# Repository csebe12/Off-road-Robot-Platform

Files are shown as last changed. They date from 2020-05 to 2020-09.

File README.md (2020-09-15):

# Off-road-Robot-Platform
This repository contains the instructions and code to set up an off-road tracked platform using DFRobot's Yuewalker chassis.

This is how the assembled robot will look like:


The webserver was developed to be mobile friendly. The following pictures show how the UI looks like on desktop (top view) and on a mobile device (bottom view).

## Control panel
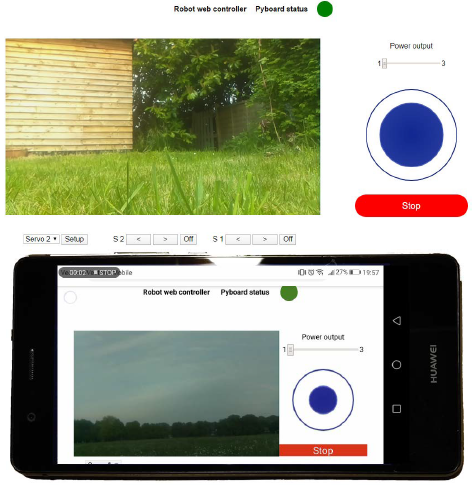
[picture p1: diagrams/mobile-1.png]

The first panel is the control panel. On the top, the green circle indicates that the UART communication between the Raspberry Pi and Pyboard works properly. If there is an error, it will turn red. The live camera feed is displayed on the left. The robot can be controlled by the blue joystick on the right. The output from the joystick is transformed into left and right motor values using the arcade mixing function. The different power settings enable precise and fast movements. On the bottom, the servos can be setup on the go. Once the user clicks setup, the servo can be plugged in into the corresponding port and it can be controlled using the two arrows. Servos can be deinitialized by clicking the off button.

## Navigation panel
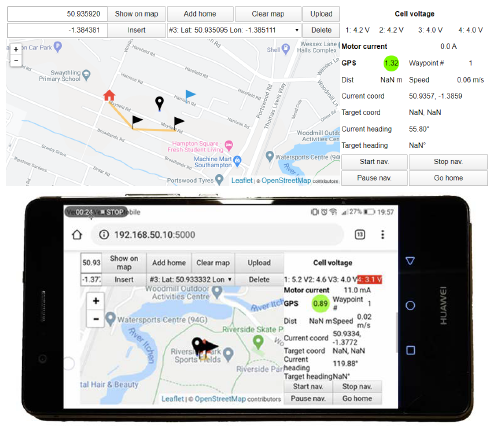
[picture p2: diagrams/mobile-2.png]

The second panel is used for setting up and monitoring the autonomous mode. The map is displayed using the Leaflet JavaScript library. The map tiles were downloaded using the RgoogleMaps package and are stored on the Raspberry Pi. This enables the users to use the map without internet connection. Waypoints can either be added by entering their latitude and longitude or simply by clicking on the map. The waypoint can then be added to the list by clicking insert. Any waypoint can be removed from or added to the list, or can be set as home. Waypoints are uploaded to the Pyboard by clicking the upload button. Data such as the battery voltage, the motor’s current consumption and navigation information are displayed on the right. When the navigation is started the bottom four buttons will have the same colours as the LEDs.

## Command history
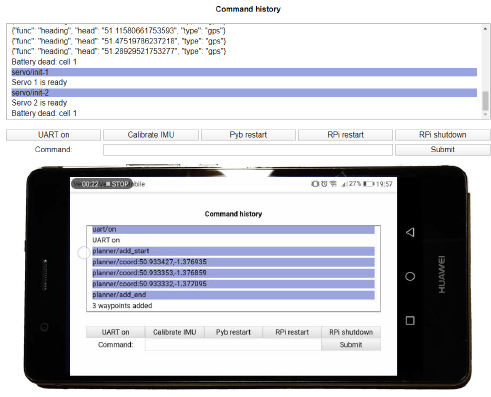
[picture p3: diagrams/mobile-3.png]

The third panel shows the command history. To distinguish between the Pyboard’s and the Rasperry Pi’s messages, those sent by the Raspberry Pi have a blue background. The most popular actions can be called by clicking the buttons, or the user can issue any command by entering it to the input box.

# Setup
## Hardware
The robot uses two MCUs, a Pyboard v1.1 and a Raspberry Pi Zero W. The latter can be exchanged to any WiFi enabled Raspberry Pi.
The schematic, layout and bill of materials to assemble the control unit can be found in the control-unit folder.
## Pyboard
The application requires threads and double precision floating points. To achieve this, the firmware needs to be updated from [the official website](https://micropython.org/download/pybv1/).
The code is located in the micropython folder. Without precompilation, its size too big to store on the Pyboard's flash, so an SD card is required.
### SD card booting
The SD card cannot be directly mounted on startup, because the buck converter cannot handle the sudden current surge. To fix this, put the pybrestart.py file on the flash. This will do a hard reset after 3 seconds. Then the SD card will be mounted.
### Files
Upload all the files from the micropython folder to the Pyboard's SD card except for the pybrestart.py
## Raspberry Pi
### [Enable I2C and SSH](https://itsfoss.com/ssh-into-raspberry/)
### Install Flask
```
sudo pip install flask + pip install -U flask-cors
```
Here are some useful flask tutorials:
* https://learn.sparkfun.com/tutorials/using-flask-to-send-data-to-a-raspberry-pi/all
* https://www.instructables.com/id/Smooth-Web-Browser-Motor-Control/
* https://pythonhow.com/add-css-to-flask-website/

### Access point
Follow [this tutorial](https://www.raspberryconnect.com/projects/65-raspberrypi-hotspot-accesspoints/168-raspberry-pi-hotspot-access-point-dhcpcd-method).
If you get at any point a "Temporary failure in name resolution" error you can fix it by running
```
sudo sh –c ‘echo “nameserver 8.8.8.8” >> /etc/resolv.conf’
```
### Files
Upload the files from the rpi folder. The script is started by running thread.py. To run it, use the following command:
```
sudo -E -H python3 thread.py
```
### Starting script on boot
Use the rc.local method with the commmand above following [this tutorial](https://www.dexterindustries.com/howto/run-a-program-on-your-raspberry-pi-at-startup/)
### Reverting to WiFi
By running wifi-access.sh you can revert back to using WiFi. Conversely, by running access-point.sh the Raspberry Pi will act as an access point. You must restart before the changes take place.
### Offline map tiles
You can save Google Maps tiles from your desired area using [this tutorial](http://rgooglemaps.r-forge.r-project.org/OfflineMaps-RgoogleMaps-leaflets.html). Once you downloaded the map tiles, save it on the Raspberry Pi in the app/static/mapTiles folder.
# Operation
Here is an overview of the components:
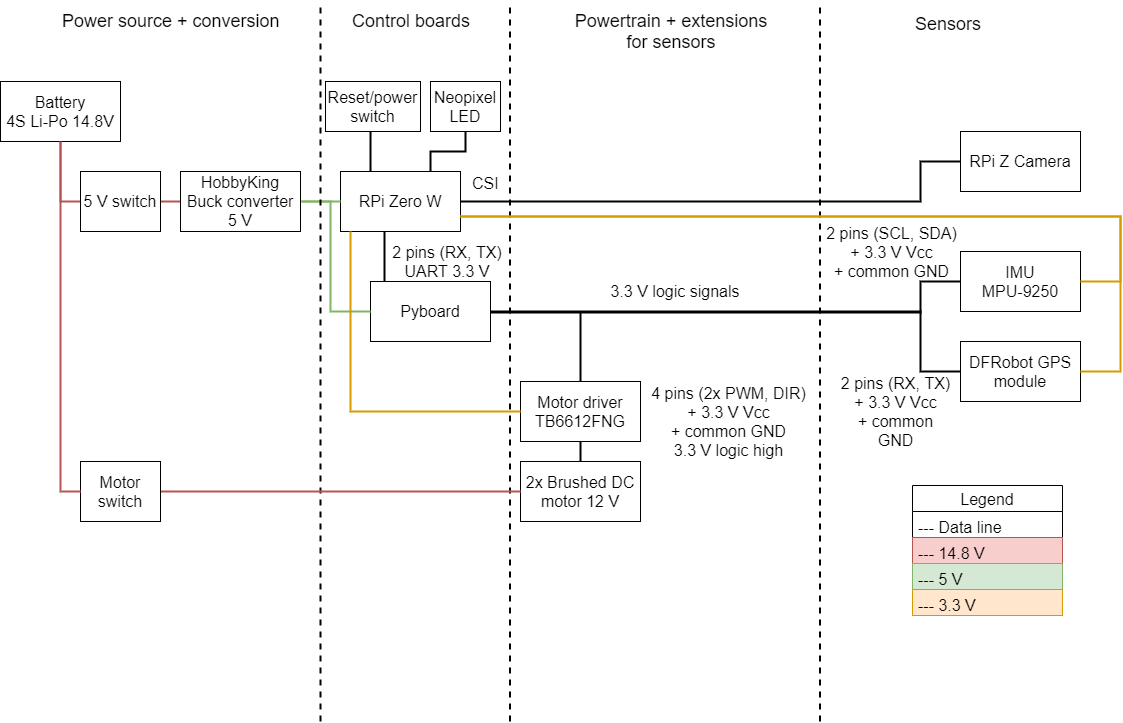
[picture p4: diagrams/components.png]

Below is the system's block diagram
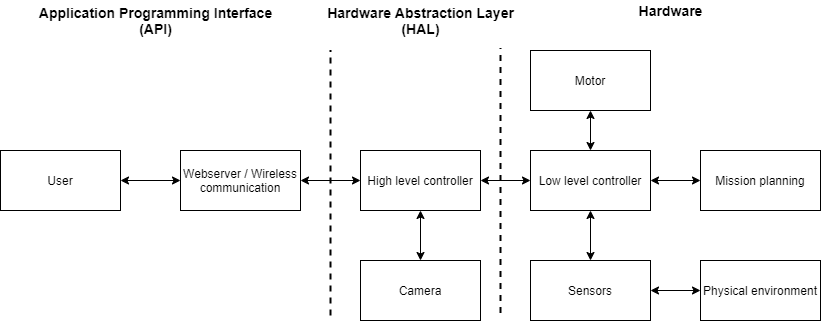
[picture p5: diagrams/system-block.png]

## Commands
To see the full list of complete commands, examine the cmd.py file in the micropython/lib directory.

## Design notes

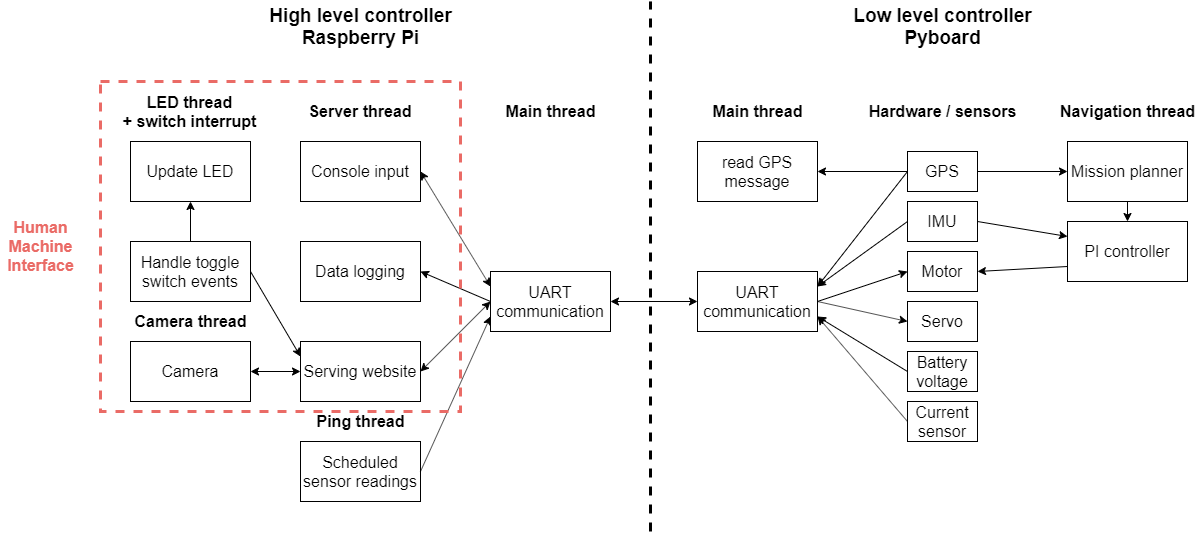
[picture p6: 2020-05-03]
diagrams/software-overview.png

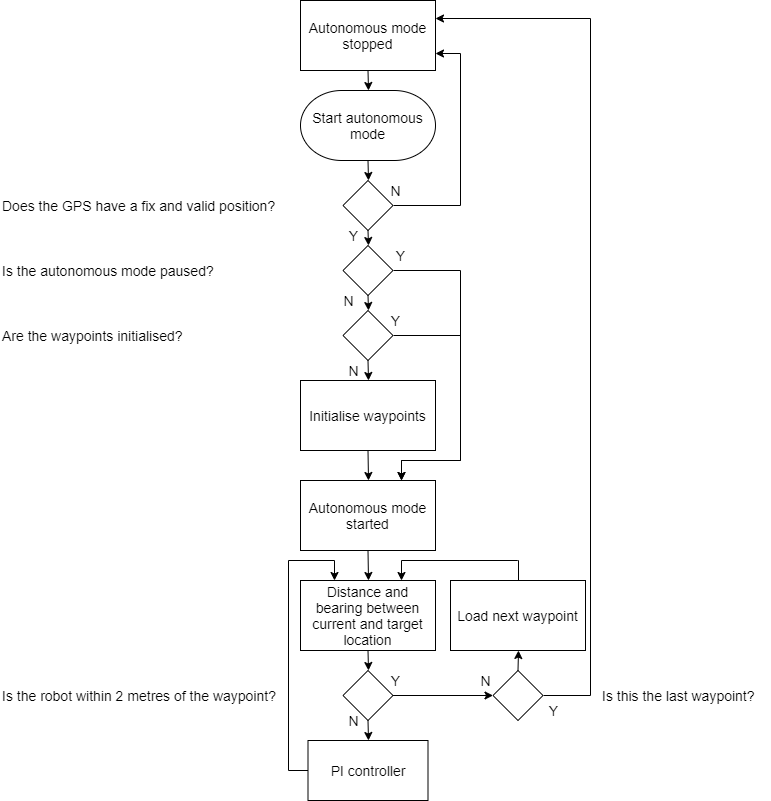
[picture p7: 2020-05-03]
diagrams/mission_planner.png

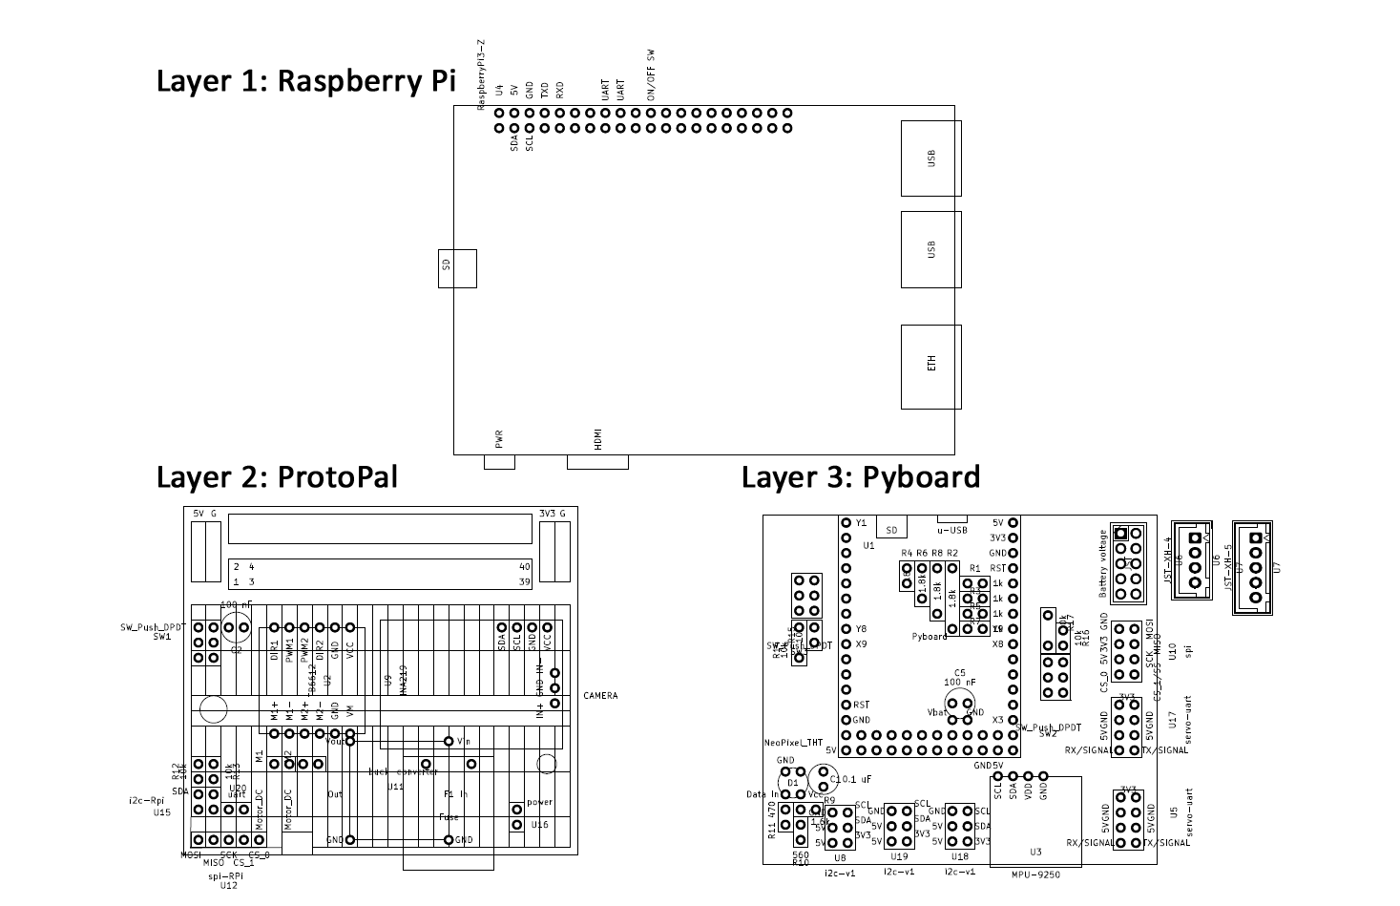
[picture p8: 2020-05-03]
control-unit/layout.png

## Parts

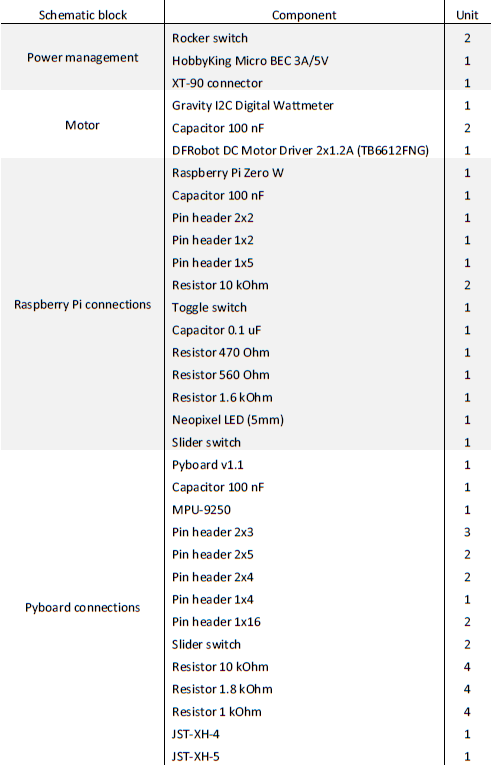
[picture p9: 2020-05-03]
control-unit/bom.png

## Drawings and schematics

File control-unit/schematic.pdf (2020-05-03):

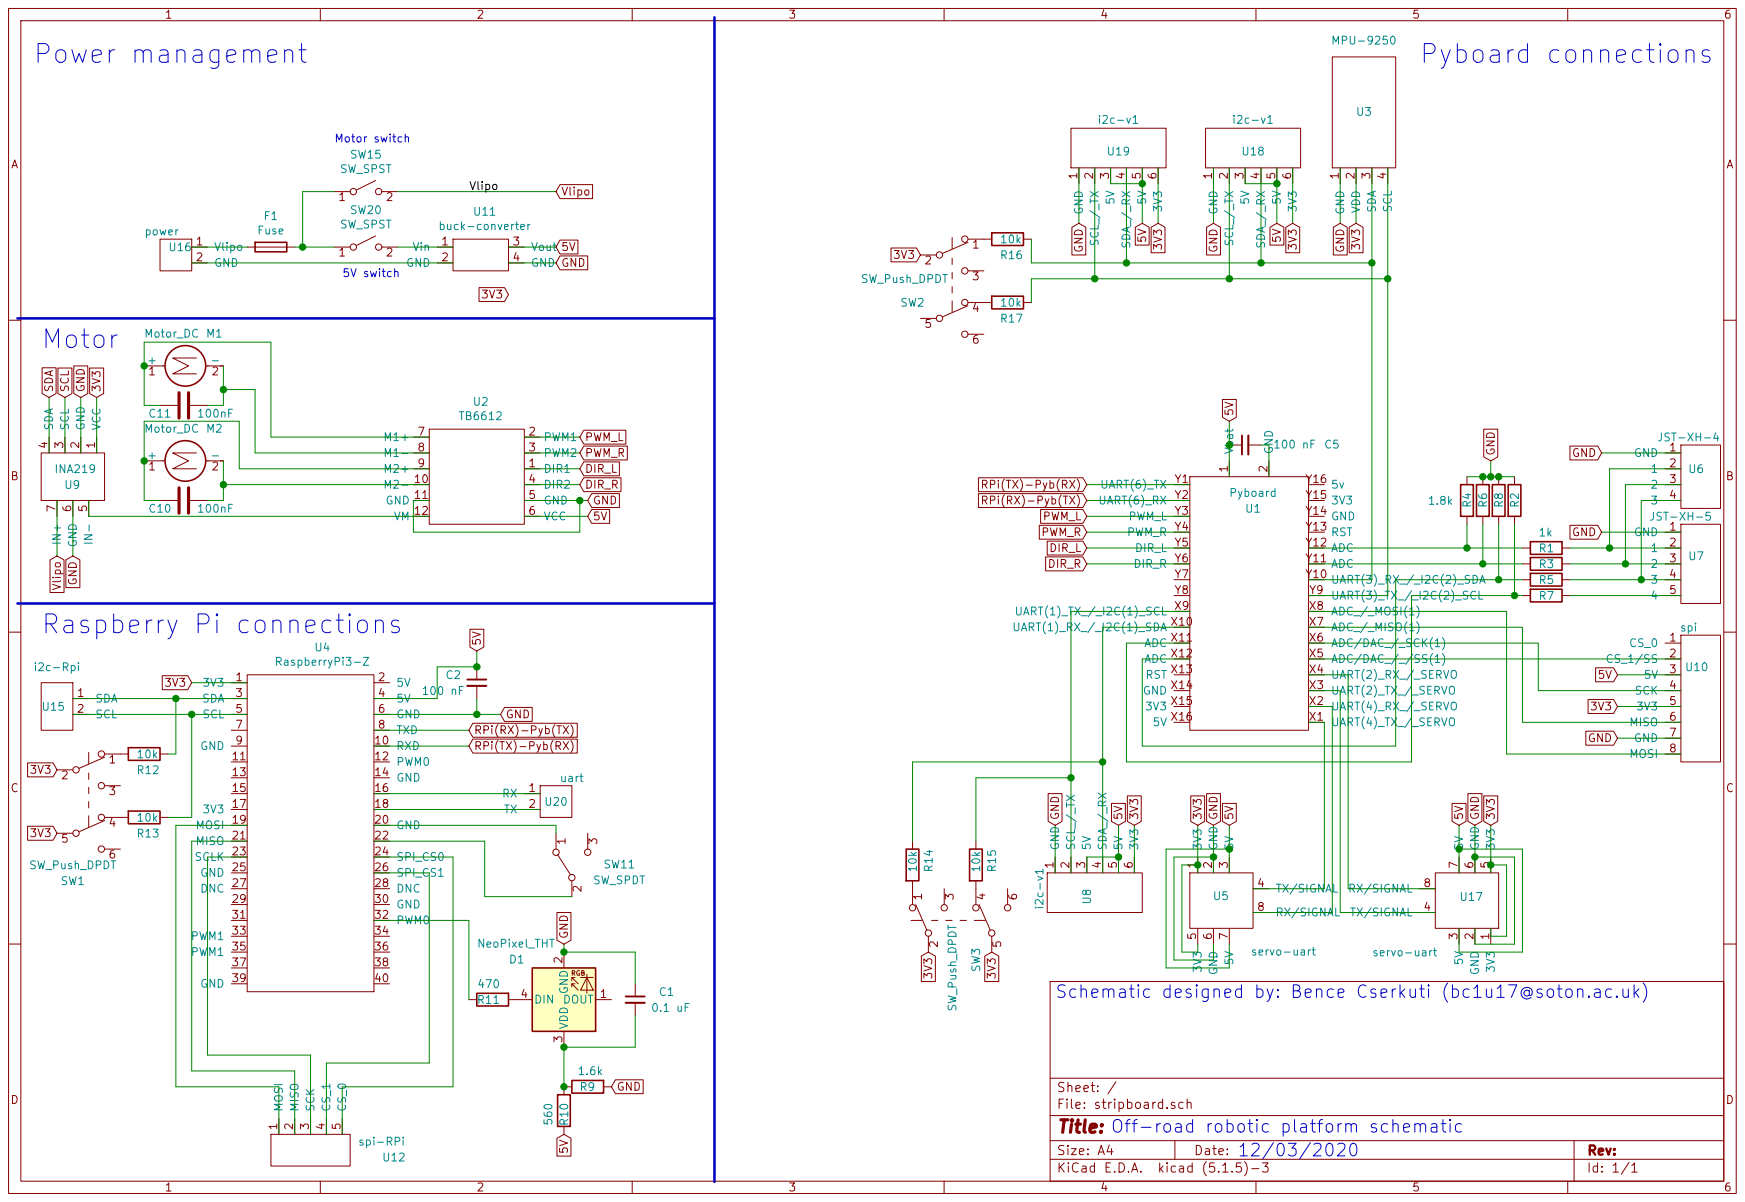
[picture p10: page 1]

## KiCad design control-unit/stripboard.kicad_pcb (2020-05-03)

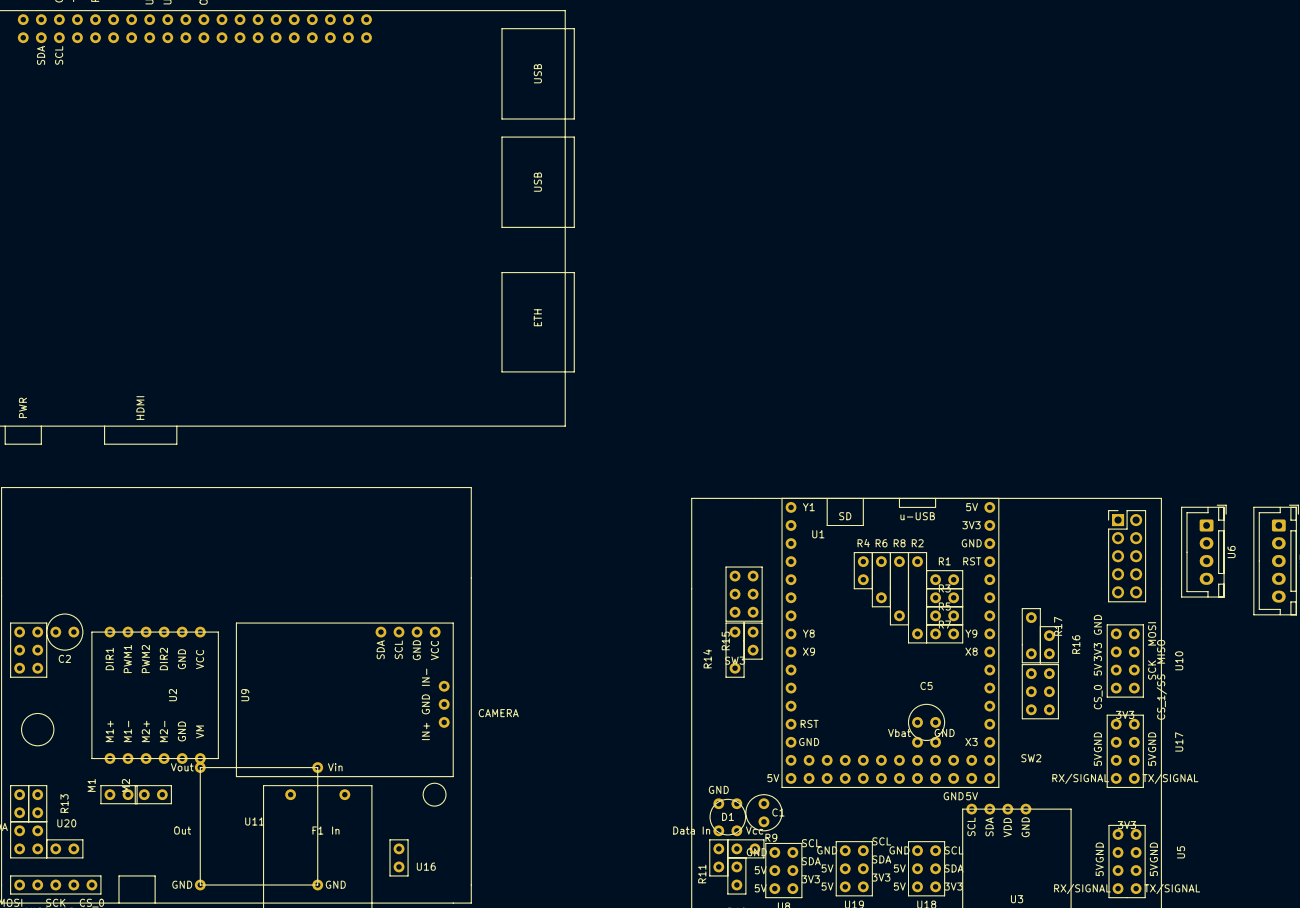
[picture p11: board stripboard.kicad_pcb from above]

Board: 2 copper layers, 46 parts (0 on the bottom side), 55 nets, no tracks yet.

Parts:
C1: 0.1 uF; capacitor
C2, C5: 100 nF; capacitor
D1: NeoPixel_THT; Neopixel
F1: Fuse; fuse
JST: Battery voltage; PinHeader_2x05_P2.54mm_Vertical
M1, M2: Motor_DC; screw-terminal
R1, R3, R5, R7: 1k; R
R2, R4, R6, R8: 1.8k; R
R9: 1.6k; R
R10: 560; R
R11: 470; R
R12, R13, R14, R15, R16, R17: 10k; R
SW1, SW2, SW3: SW_Push_DPDT; dpdt
U1: Pyboard
U2: TB6612
U3: MPU-9250
U4: RaspberryPi3-Z; Raspberry Pi 3 Model B
U5, U17: servo-uart
U6: JST-XH-4; JST_XH_B4B-XH-A_1x04_P2.50mm_Vertical
U7: JST-XH-5; JST_XH_B5B-XH-A_1x05_P2.50mm_Vertical
U8, U18, U19: i2c-v1
U9: INA219
U10: spi
U11: buck-converter; buck converter
U12: spi-RPi
U15: i2c-Rpi; i2c Rpi
U16: power; screw-terminal
U20: uart

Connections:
3V3: SW1.2, SW1.5, SW2.2, SW2.5, SW3.2, SW3.5, U3.2, U4.1, U5.1, U8.6, U9.1, U10.5, U17.1, U17.5, U18.6, U19.6
5V: C2.1, C5.1, R10.1, U1.1, U2.6, U4.4, U5.3, U8.3, U8.5, U10.3, U11.3, U17.3, U17.7, U18.3, U18.5, U19.3, U19.5
GND: C1.1, C2.2, D1.2, R2.1, R4.1, R6.1, R8.1, R9.2, U2.5, U2.11, U3.1, U4.6, U5.2, U6.1, U7.1, U8.1, U9.2, U9.6, U10.7, U11.4, U17.2, U17.6, U18.1, U19.1
unnamed: C1.2, D1.3, R9.1, R10.2
unnamed: C5.2, U1.2
unnamed: D1.4, R11.2
unnamed: F1.2, U16.1
unnamed: M1.1, U2.7
unnamed: M1.2, U2.8
unnamed: M2.1, U2.9
unnamed: M2.2, U2.10
unnamed: R1.1, U6.2, U7.2
unnamed: R1.2, R4.2, U1.Y12
unnamed: R2.2, R7.2, U1.X11
unnamed: R3.1, U6.3, U7.3
unnamed: R3.2, R6.2, U1.Y11
unnamed: R5.1, U6.4, U7.4
unnamed: R5.2, R8.2, U1.X12
unnamed: R7.1, U7.5
unnamed: R11.1, U1.Y7
unnamed: R12.1, U4.3, U15.1
unnamed: R12.2, SW1.1
unnamed: R13.1, U4.5, U15.2
unnamed: R13.2, SW1.4
unnamed: R14.1, U1.X10, U8.4
unnamed: R14.2, SW3.1
unnamed: R15.1, U1.X9, U8.2
unnamed: R15.2, SW3.4
unnamed: R16.1, U1.Y9, U3.4, U9.3, U18.2, U19.2
unnamed: R16.2, SW2.1
unnamed: R17.1, U1.Y10, U3.3, U9.4, U18.4, U19.4
unnamed: R17.2, SW2.4
unnamed: U1.X1, U5.4
unnamed: U1.X2, U5.8
unnamed: U1.X3, U17.4
unnamed: U1.X4, U17.8
unnamed: U1.X5, U10.2
unnamed: U1.X6, U10.4
unnamed: U1.X7, U10.6
unnamed: U1.X8, U10.8
unnamed: U1.Y3, U2.2
unnamed: U1.Y4, U2.3
unnamed: U1.Y5, U2.1
unnamed: U1.Y6, U2.4
unnamed: U2.12, U9.5
unnamed: U11.2, U16.2
unnamed: U4.19, U12.1
unnamed: U4.21, U12.2
unnamed: U4.23, U12.3
unnamed: U4.26, U12.4
unnamed: U4.24, U12.5
unnamed: U4.16, U20.1
unnamed: U4.18, U20.2
RPi(RX)-Pyb(TX): U1.Y2, U4.8
RPi(TX)-Pyb(RX): U1.Y1, U4.10

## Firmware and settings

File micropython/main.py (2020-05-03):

import _thread
import global_variables
import cmd
import sensors
from utime import ticks_ms, ticks_diff, sleep_ms
import gc

def main():
    global_variables.init()
    print('Board initialised')
    # _thread.start_new_thread(sensors.fusion_read, ())
    _thread.start_new_thread(global_variables.pid_test.start_pid, ())

    i = 0
    while True:
        if global_variables.uart.any() > 0:
            cmd.command()
        elif global_variables.uart_gps.any() > 0:
            global_variables.gps_device.update()
        i += 1
        if i % 100 == 0:
            gc.collect()


        # if i % 20 == 0:
        #     gc.collect()
        # i += 1
        # if i % 5 == 0:
        #     print("Heading, Pitch, Roll: {:7.3f} {:7.3f} {:7.3f}".format(global_variables.fuse.heading, global_variables.fuse.pitch, global_variables.fuse.roll))
        # sleep_ms(20)
        # i += 1


if __name__ == '__main__':
    main()

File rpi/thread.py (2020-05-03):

#!/usr/bin/env python3
import threading
import sys
from signal import signal, SIGINT
sys.path.insert(1, '/home/pi/Desktop/app')
import web_server
import comms
import console
import global_vars
from time import sleep


def handler(signal_received, frame):
	print("\nCtrl + C detected, closing files")
	comms.uart_close()
	comms.log_close()
	global_vars.np.deinit()

	exit(0)

def server_uart():
	try:
		comms.uart_init()
		comms.log_init()
		web_server.server()
	finally:
		comms.uart_close()
		comms.log_close()
		global_vars.np.deinit()

def main():
	signal(SIGINT, handler)

	global_vars.init()
	server_thread = threading.Thread(target=server_uart, args=())
	console_thread = threading.Thread(target=console.console_input, args=())
	ping_thread = threading.Timer(3, comms.ping)
	led_thread = threading.Thread(target=global_vars.led_thread, args=())
	
	server_thread.start()
	console_thread.start()
	ping_thread.start()
	led_thread.start()
	global_vars.led(freq=1, color=(40, 110, 222), alternate_color=(40, 110, 222))
	while True:
		comms.uart_read()
	
	
if __name__ == "__main__":
	main()

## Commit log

2020-05-03 Repository folder update
    [stripboard.kicad_pcb, stripboard.sch]
2020-05-08 Bug fixes for autonomous mode
    [comms.py]
